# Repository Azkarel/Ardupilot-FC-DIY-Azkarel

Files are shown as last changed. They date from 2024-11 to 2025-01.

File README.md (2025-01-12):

# Ardupilot-FC-DIY-Azkarel

DIY Flight Controller for Ardupilot based on STM32H743 developer board

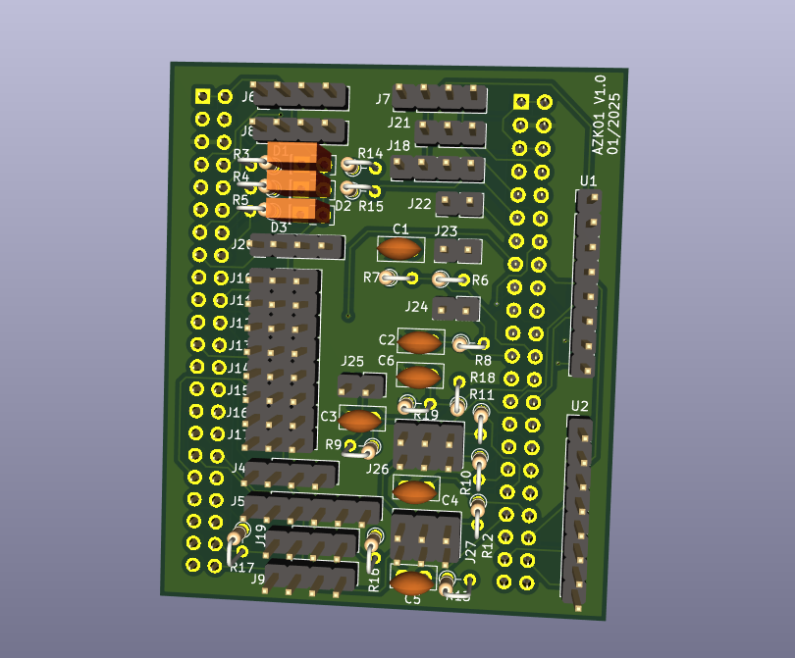
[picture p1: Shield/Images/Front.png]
AzkarelFC_Board Azkarel_Pinout


## Features

 - STM32H743 microcontroller
 - Two IMUs: MPU-9250, ICM20948
 - Two Magnetometers included in IMUs: AK8963, AK09916
 - Two Barometers: BMP-280, BMP-388
 - Internal vibration isolation for IMUs
 - Internal RGB LED
 - MicroSD card slot port
 - 1 USB port
 - 4 UARTs ports
 - 2 I2C and 1 CAN ports
 - 8 PWM output ports
 - Safety switch port
 - Buzzer port
 - RC IN port
 - SBUS/DSM port

## Pinout
AzkarelFC_Board Azkarel_Pinout

## Connectors

**GPS1**

| Pin  | Signal  | Volt  |
| :--: | :-----: | :---: |
|  1 | RX | +3.3V |
|  2 | 5V |  +5V  |
|  3 | GND |  GND  |
|  4 | TX | +3.3V |

**GPS2**

| Pin  | Signal  | Volt  |
| :--: | :-----: | :---: |
|  1 | RX | +3.3V |
|  2 | 5V |  +5V  |
|  3 | GND |  GND  |
|  4 | TX | +3.3V |

**HEATER**

| Pin  | Signal  | Volt  |
| :--: | :-----: | :---: |
|  1 |HEATER_EN| +3.3V |
|  2 | 5V |  +5V  |
|  3 | GND |  GND  |
|  4 | - |  - |

**BUZZER**

| Pin  | Signal | Volt  |
| :--: | :----: | :---: |
|  1 | 5V |  +5V  |
|  2 | GND  |  GND  |
|  3 | BUZZER | +3.3V |

**I2C2**

| Pin  | Signal  | Volt  |
| :--: | :-----: | :---: |
|  1 | I2C_SCL | +3.3V |
|  2 | 5V |  +5V  |
|  3 | GND |  GND  |
|  4 | I2C_SDA | +3.3V |

**RCINT**

| Pin  | Signal  | Volt  |
| :--: | :-----: | :---: |
|  1 |  RC_INT | +3.3V |
|  2 | 5V |  +5V  |
|  3 | GND |  GND  |
|  4 | - | - |

**PWM 1 to 8**

| Pin  |  Signal  | Volt  |
| :--: | :---: | :---: |
|  1 |  SIGNAL  | +3.3V |
|  2 | VCC |  +5V  |
|  3 | GND |  GND  |

**ADC_6V6**

| Pin  |  Signal  | Volt  |
| :--: | :---: | :---: |
|  1 | GND |  GND  |
|  2 |  SIGNAL  | +6.6V |

**ADC_3V3**

| Pin  |  Signal  | Volt  |
| :--: | :---: | :---: |
|  1 | GND |  GND  |
|  2 |  SIGNAL  | +3.3V |

**RSSI_IN**

| Pin  |  Signal  | Volt  |
| :--: | :---: | :---: |
|  1 | GND |  GND  |
|  2 |  SIGNAL  | +3.3V |

**SAFETY_LED**

| Pin  | Signal | Volt  |
| :--: | :---: | :---: |
|  1 | 5V_OUT |  +5V  |
|  2 | GND |  GND  |
|  3 | SAFETY_SW_LED | +3.3V |

**SAFETY_SW**

| Pin  | Signal | Volt  |
| :--: | :---: | :---: |
|  1 | 5V_OUT |  +5V  |
|  2 | GND |  GND  |
|  3 | SAFETY_SW | +3.3V |

**TELEM1**

| Pin  | Signal  | Volt  |
| :--: | :-----: | :---: |
|  1 | RX | +3.3V |
|  2 | 5V |  +5V  |
|  3 | GND |  GND  |
|  4 | TX | +3.3V |

**TELEM2**

| Pin  | Signal  | Volt  |
| :--: | :-----: | :---: |
|  1 | RX | +3.3V |
|  2 | TX | +3.3V |
|  3 | 5V |  +5V  |
|  4 | GND |  GND  |
|  5 | RTS | +3.3V |
|  6 | CTS | +3.3V |

**BATTERY_VOLTAGE**

| Pin  | Signal | Volt  |
| :--: | :---: | :---: |
|  1 | +5V |  GND  |
|  2 | GND |  GND  |
|  3 | BAT_VOLTAGE_ADC | +3.3V |

**BATTERY_CURRENT**

| Pin  | Signal | Volt  |
| :--: | :---: | :---: |
|  1 | +5V |  GND  |
|  2 | GND |  GND  |
|  3 | BAT_CRRENT_ADC  | +3.3V |

**I2C4**

| Pin  | Signal  | Volt  |
| :--: | :-----: | :---: |
|  1 | I2C_SCL | +3.3V |
|  2 | 5V |  +5V  |
|  3 | GND |  GND  |
|  4 | I2C_SDA | +3.3V |

**SBUS/DSM**

| Pin  | Signal  | Volt  |
| :--: | :-----: | :---: |
|  1 | RX | +3.3V |
|  2 | 5V |  +5V  |
|  3 | GND |  GND  |
|  4 | TX | +3.3V |

**USB EX**

| Pin  | Signal | Volt  |
| :--: | :----: | :---: |
|  1 | VCC_IN |  +5V  |
|  2 | DM | +3.3V |
|  3 | DP | +3.3V |
|  4 |  GND |  GND  |

## UART Mapping

 - SERIAL0 -> USB(OTG1)
 - SERIAL1 -> USART1(Telem1)
 - SERIAL2 -> USART2 (Telem2)
 - SERIAL3 -> USART3 (GPS1), NODMA
 - SERIAL4 -> UART5 (GPS2), NODMA
 - SERIAL5 -> UART8 (SBUS)
 - SERIAL6 -> UART7 (Debug), NODMA
 - SERIAL7 -> USB2(OTG2)

## RC Input

The remote control signal should be connected to the “RC IN” pin, in their specific connector.

This signal pin supports two types of remote control signal inputs, SBUS and PPM signals.

## PWM Output

The flight controller supports up to 8 PWM outputs, support all PWM protocols as well as DShot. All 8 PWM outputs have GND on the bottom row, 5V on the middle row and signal on the top row. 5V pins serves as feeding voltage for the FC from motor ESCs.

The 8 PWM outputs are in 2 groups:

 - PWM 1, 2, 3 and 4 in group1
 - PWM 5, 6, 7 and 8 in group2

Channels 1, 3, 5, 7 support bi-directional Dshot, channels 2, 4, 6, 8 support Dshot.

## Battery Monitoring

The flight controller has two connectors to monitorize voltage and current from battery.

## GPIOs

All 8 PWM channels can be used for GPIO functions (relays, buttons, RPM etc).

The pin numbers for these PWM channels in ArduPilot are shown below:

| PWM Channels | Pin  | PWM Channels | Pin  |
| --- | ---- | --- | ---- |
| PWM1 | 50 | PWM5 | 54 |
| PWM2 | 51 | PWM6 | 55 |
| PWM3 | 52 | PWM7 | 56 |
| PWM4 | 53 | PWM8 | 67 |

## Analog inputs

The flight controller has 5 analog inputs

 - ADC 5V Sense 
 - ADC Battery Current 
 - ADC Battery Voltage 
 - ADC 3V3 Sense
 - ADC 6V6 Sense
 - RSSI voltage monitoring

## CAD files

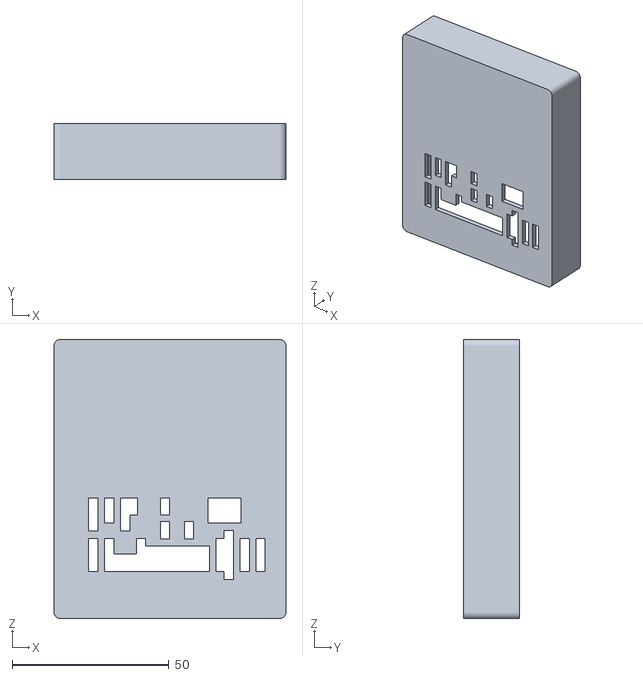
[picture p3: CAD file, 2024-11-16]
3DPrints/Tapa.STL
74.0 x 18.0 x 89.0

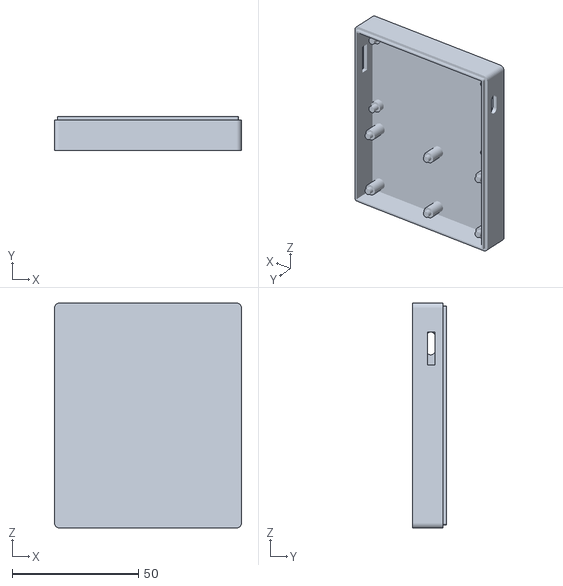
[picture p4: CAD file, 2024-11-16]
3DPrints/Base.STL
74.0 x 13.5 x 89.0

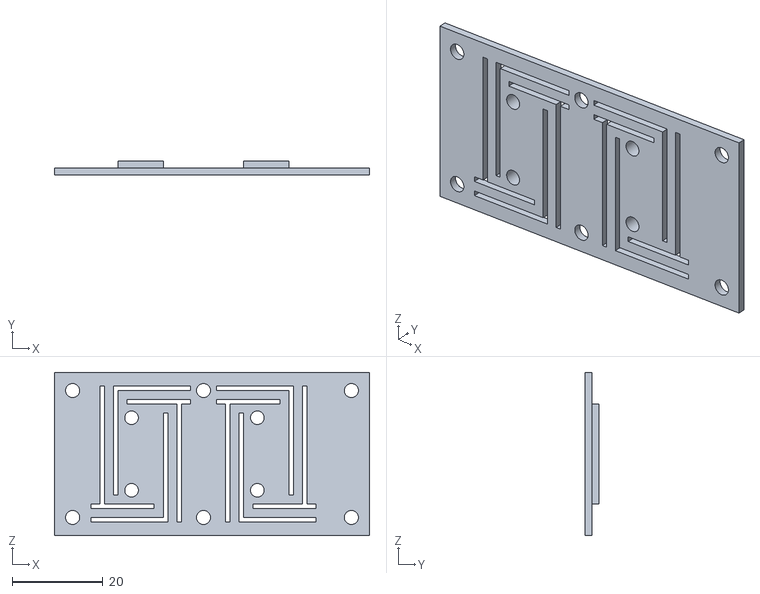
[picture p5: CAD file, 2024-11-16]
3DPrints/IMUS.STL
69.5 x 3.00 x 36.0

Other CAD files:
Shield/Shield.dxf

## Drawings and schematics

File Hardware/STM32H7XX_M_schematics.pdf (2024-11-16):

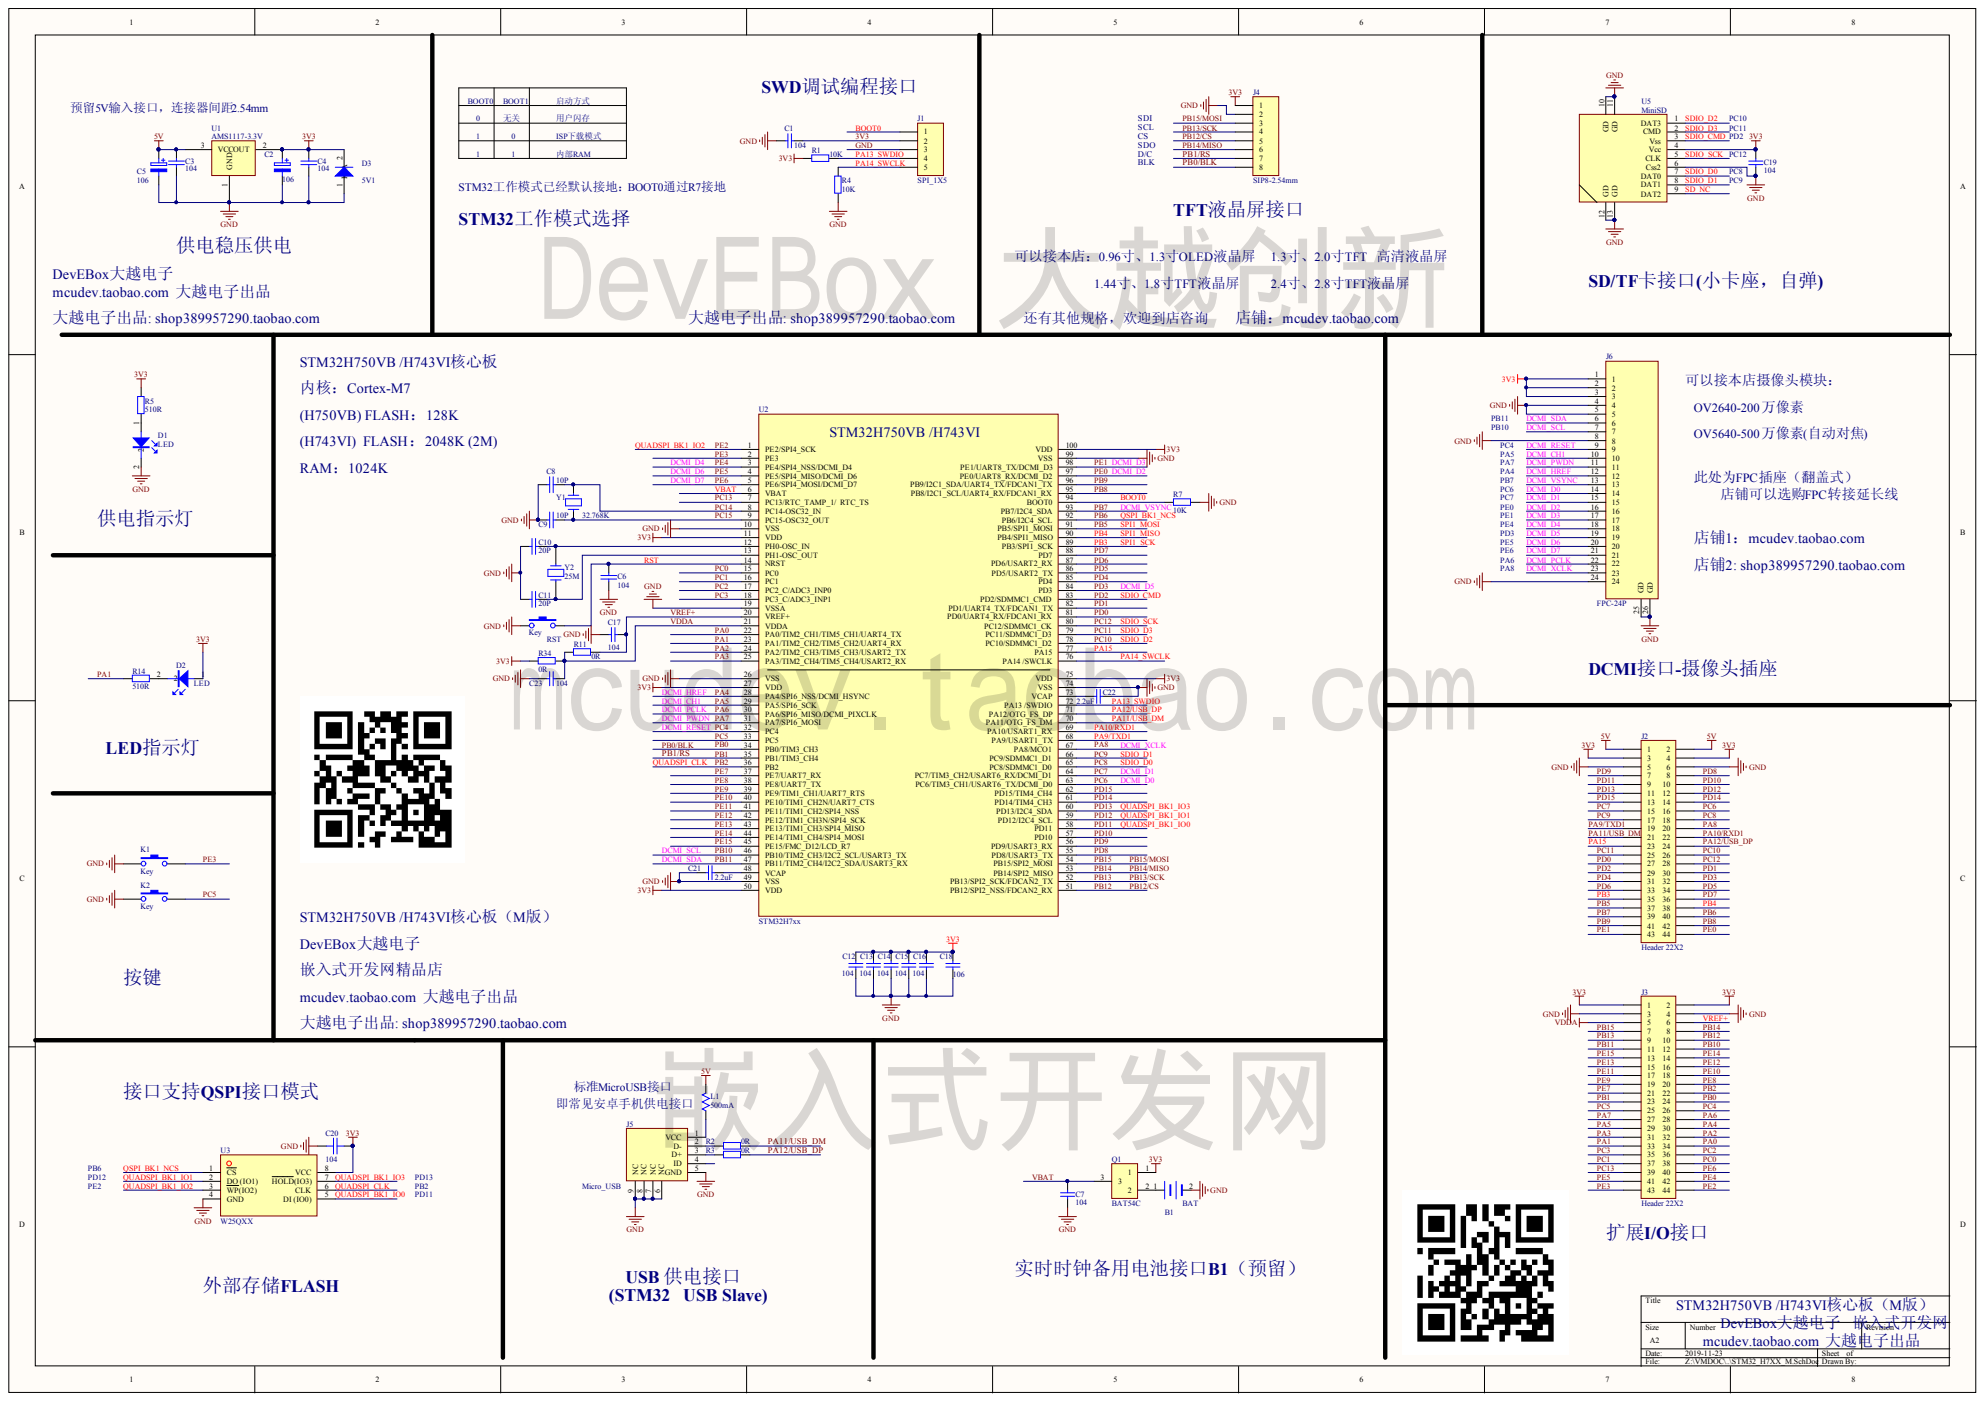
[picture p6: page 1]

GND | VSSA 19 | PD1

VCAP 48 VSS 49 | PB14

mcudev.taobao.com 大越电子出品

DevEBox大越电子

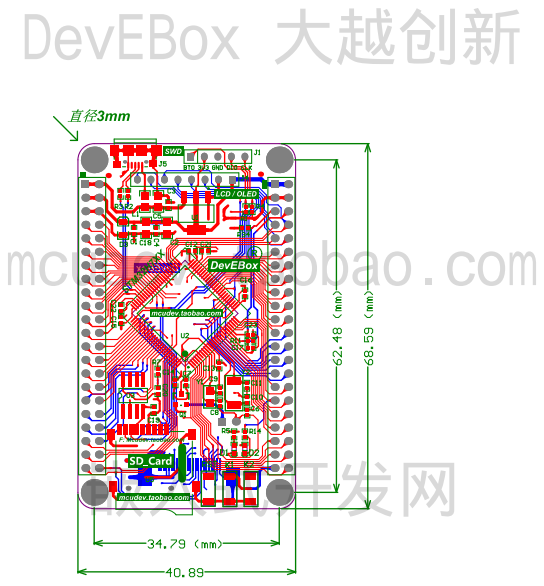
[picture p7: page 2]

Bill of Materials | <Parameter Title not found>
Source Data From: | STM32_H7XX_M.PrjPcb
Project: | | STM32_H7XX_M.PrjPcb
Variant: | | None
Creation Date: 2019-11-23 | 下午 01:44:44
Print Date: | 43792 | 43792.57279
Footprint | Comment | LibRef | Designator | Description | Quantity
SIP2-2.54mm | BAT | BATTERY | B1 | 1
RC0402 | 104 | Cap, CAP, CAP, CAP, Cap, Cap, Cap, Cap, Cap, Cap, Cap, Cap Semi, CAP, Cap | C1, C3, C4, C6, C7, C12, C13, C14, C15, C16, C17, C19, C20, C23 | Capacitor, Capacitor, Capacitor, Capacitor, Capacitor, Capacitor, Capacitor, Capacitor, Capacitor, Capacitor, Capacitor, Capacitor (Semiconductor SIM Model), [NoValue], Capacitor
14
RC0805 | 106 | ELECTRO2,
ELECTRO2,

# Cap

C2, C5, C18 | [NoValue], [NoValue], Capacitor | 3
RC0402 | 10P | CAP | C8, C9 | | 2
RC0402 | 20P | CAP | C10, C11 | Capacitor | 2
RC0603 | 2.2uF | Cap | C21, C22 | Capacitor | 2
LED-0603 | LED | LED | D1, D2 | | 2
SOD_323 | 5V1 | Diode | D3 | Default Diode | 1
SIP5-2.54mm | SPI_1X5 | Header 5H | J1 | Header, 5-Pin, Right Angle | 1
IDE2X22 | Header 22X2 | Header 22X2 | J2, J3 | Header, 22-Pin, Dual row | 2
HDR1X8 | SIP8-2.54mm | Header 8 | J4 | Header, 8-Pin | 1
micro_USB | Micro_USB | MiniUSB | J5 | | 1
FPC24- 05MM | FPC-24P | FPC-24P | J6 | | 1
SW-SPST | Key | SW-PB | K1, K2, RST | | 3
RC0805 | 500mA | RES | L1 | | 1
SOT-23- BAT54C | BAT54C | BAT54C | Q1 | | 1
RC0402 | 10K | Res2 | R1, R4, R7 | Resistor | 3
RC0402 | 0R | Res2 | R2, R3, R11, R34 | Resistor | 4
RC0402 | 510R | Res2 | R5, R14 | Resistor | 2
SOT-223 | AMS1117-3.3V | 11 | U1 | | 1
| STM32H7xx | STM32H750V | U2 | | 1
SOP8L | W25QXX | W25QXX | U3 | | 1
| MiniSD | MiniSD | U5 | | 1
JZ3215-32K | 32.768K | CRYSTAL | Y1 | 晶振 | 1
JZ5032-8M | 25M | CRYSTAL | Y2 | Crystal | 1
| | | | | 53
Approved | | Notes

# DevEBox 大越创新

# mcudev.taobao.com

# 嵌入式开发网

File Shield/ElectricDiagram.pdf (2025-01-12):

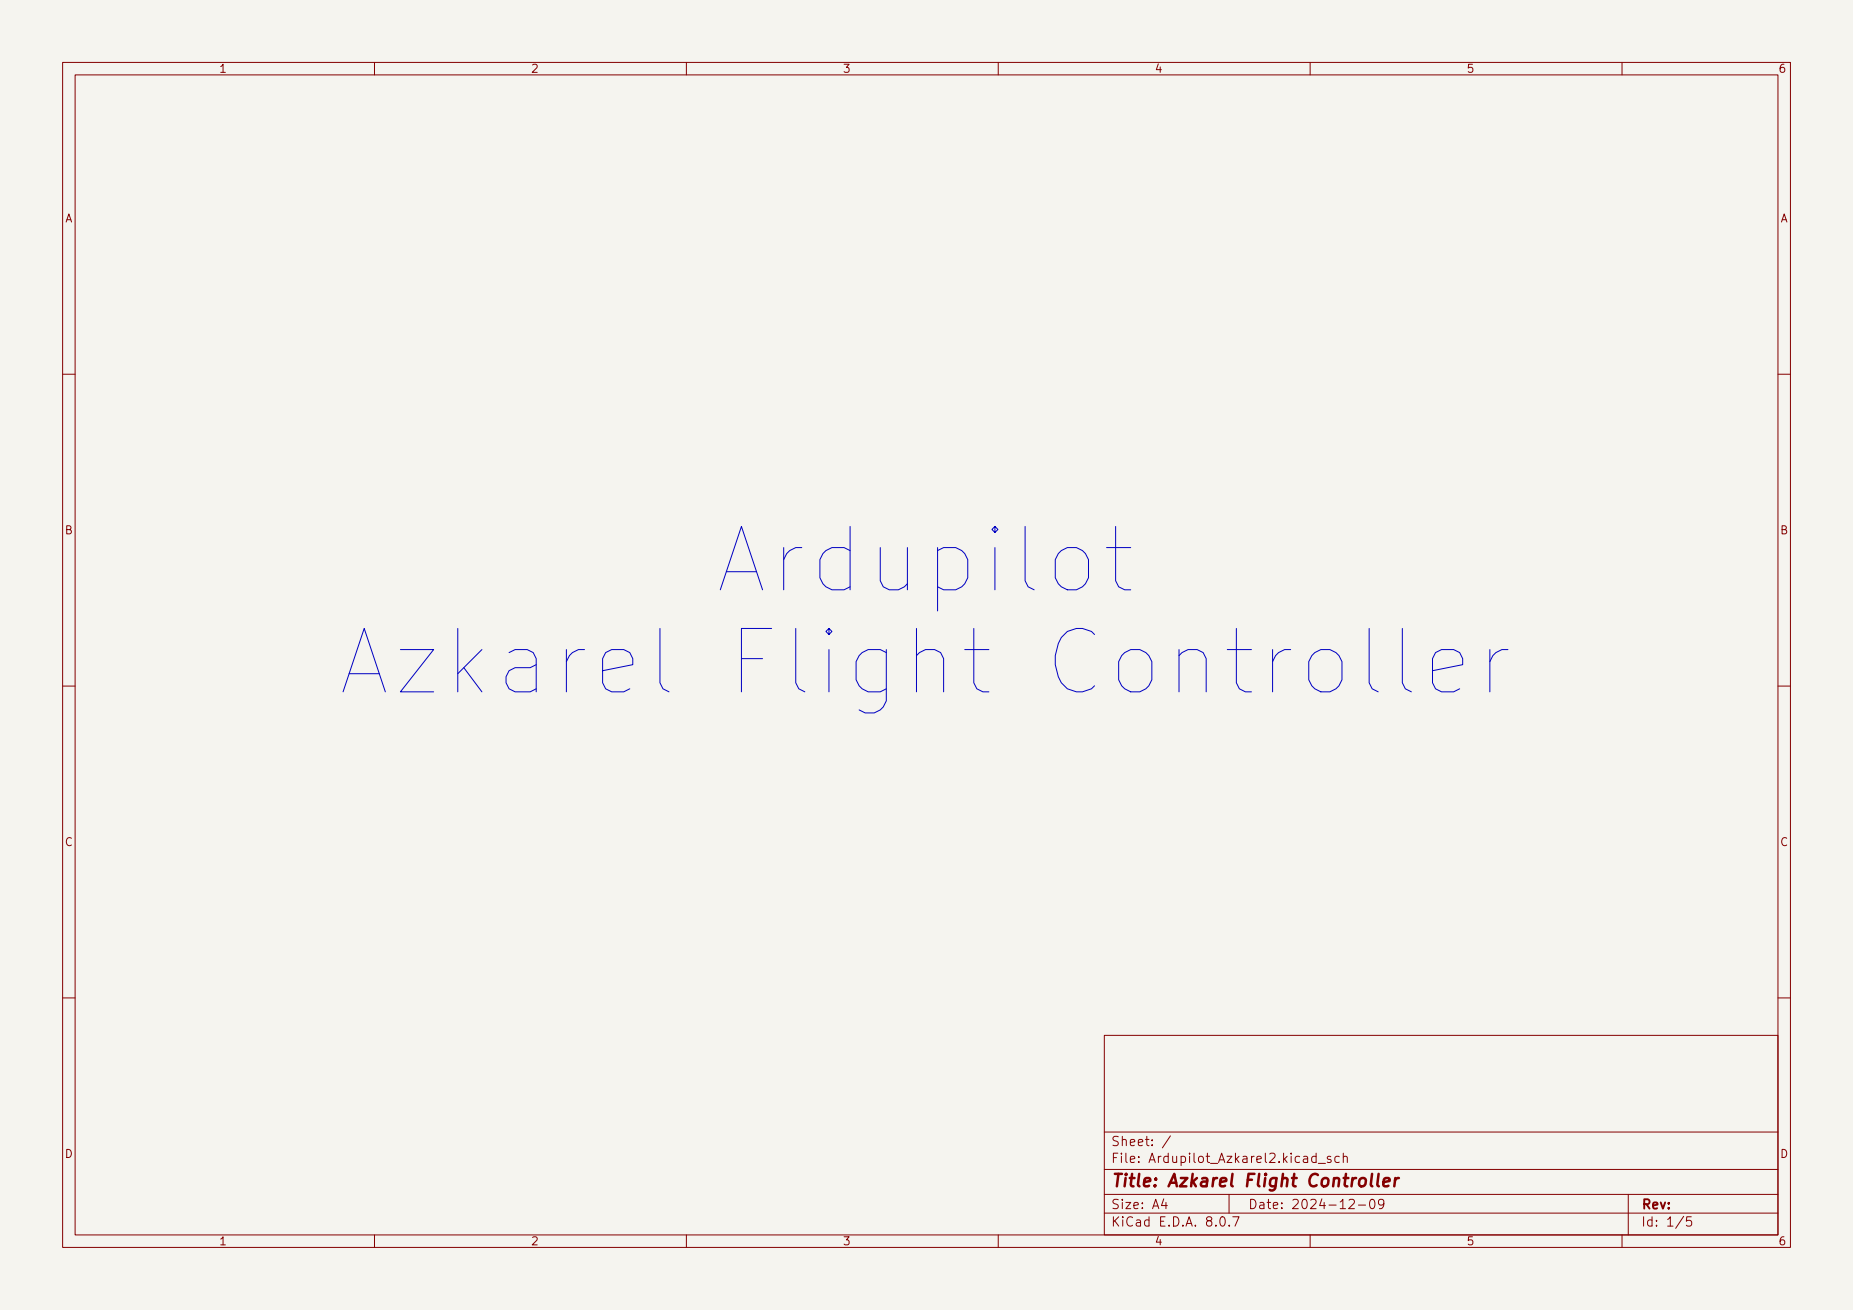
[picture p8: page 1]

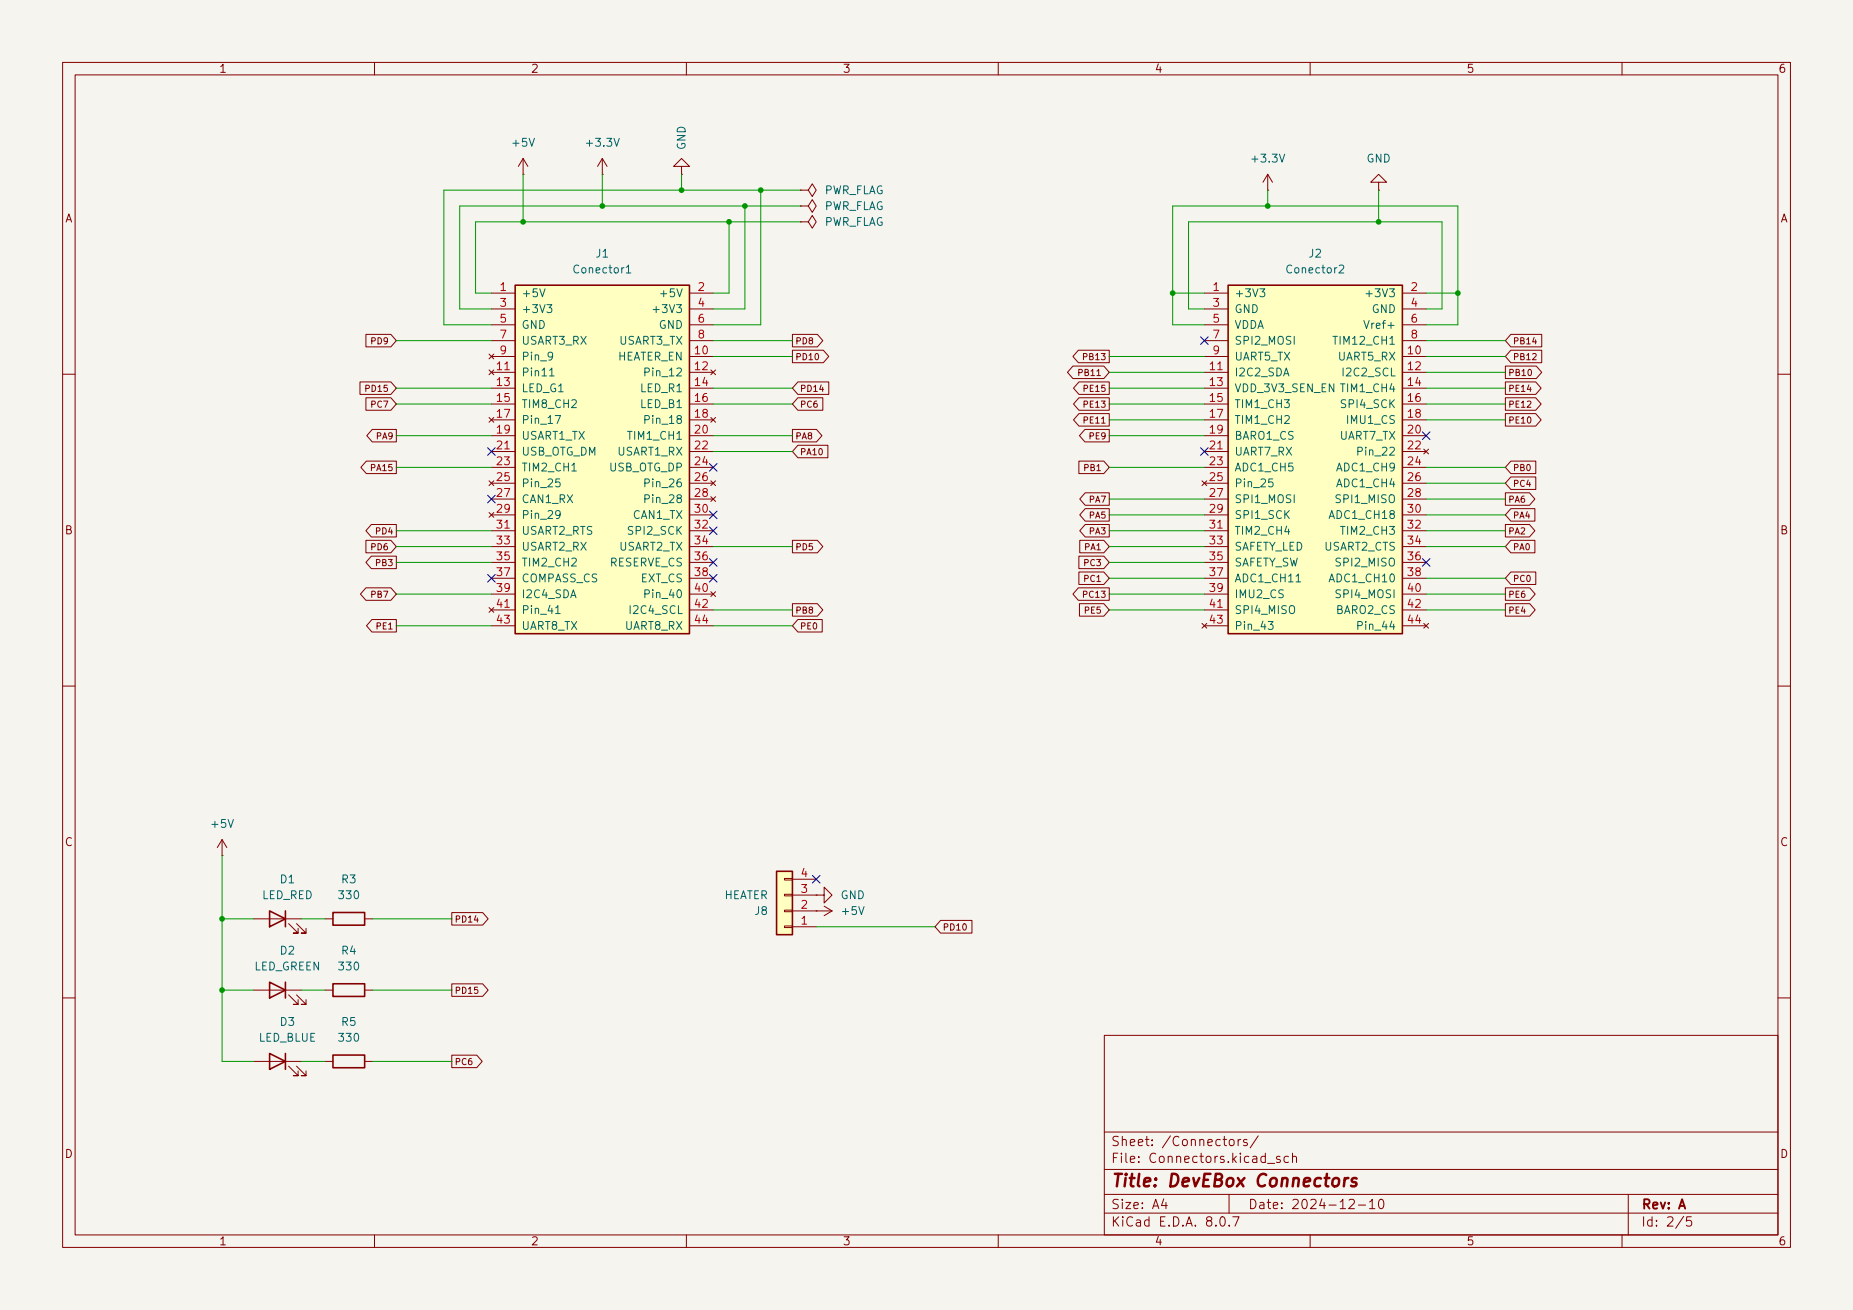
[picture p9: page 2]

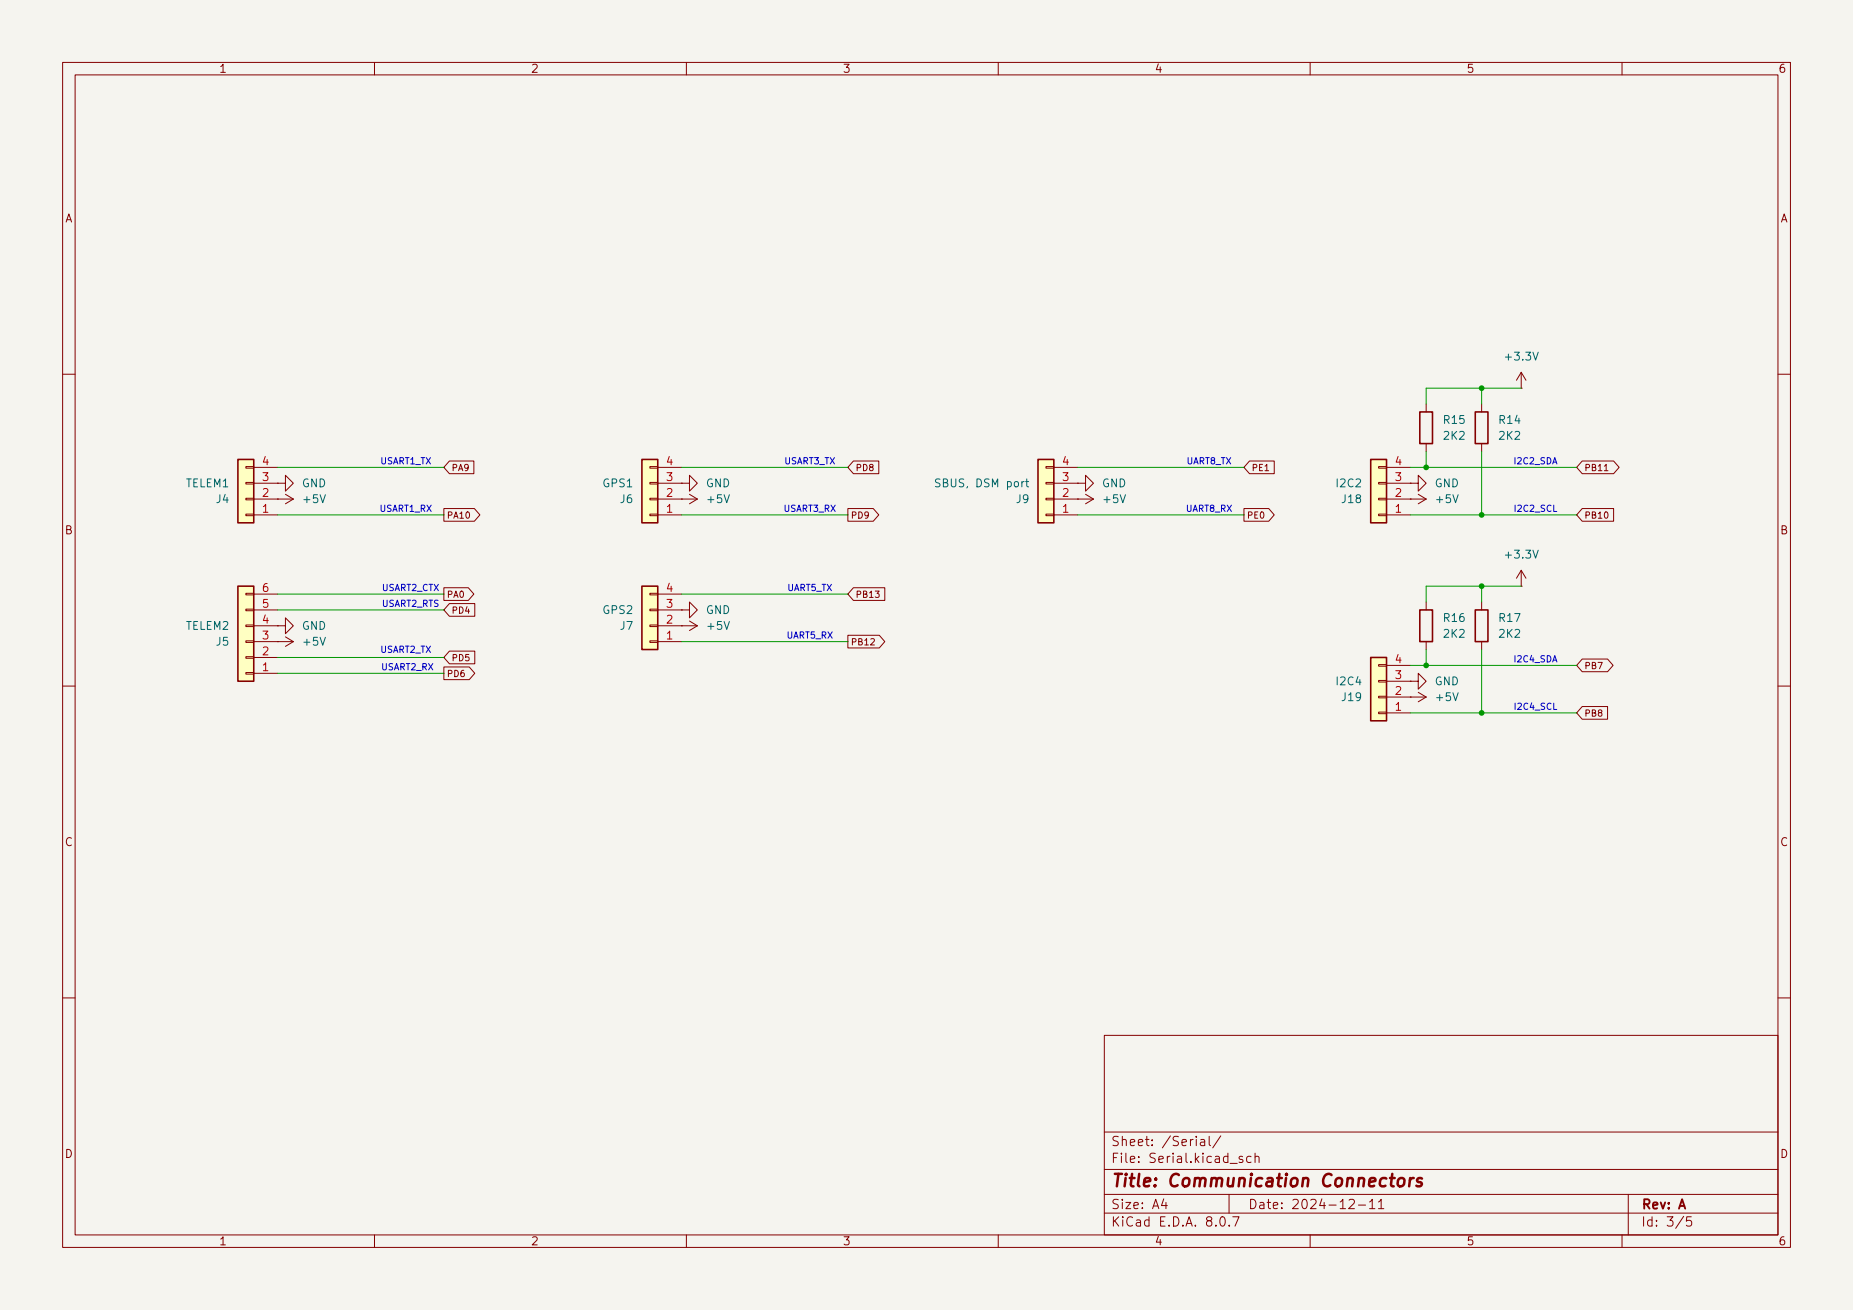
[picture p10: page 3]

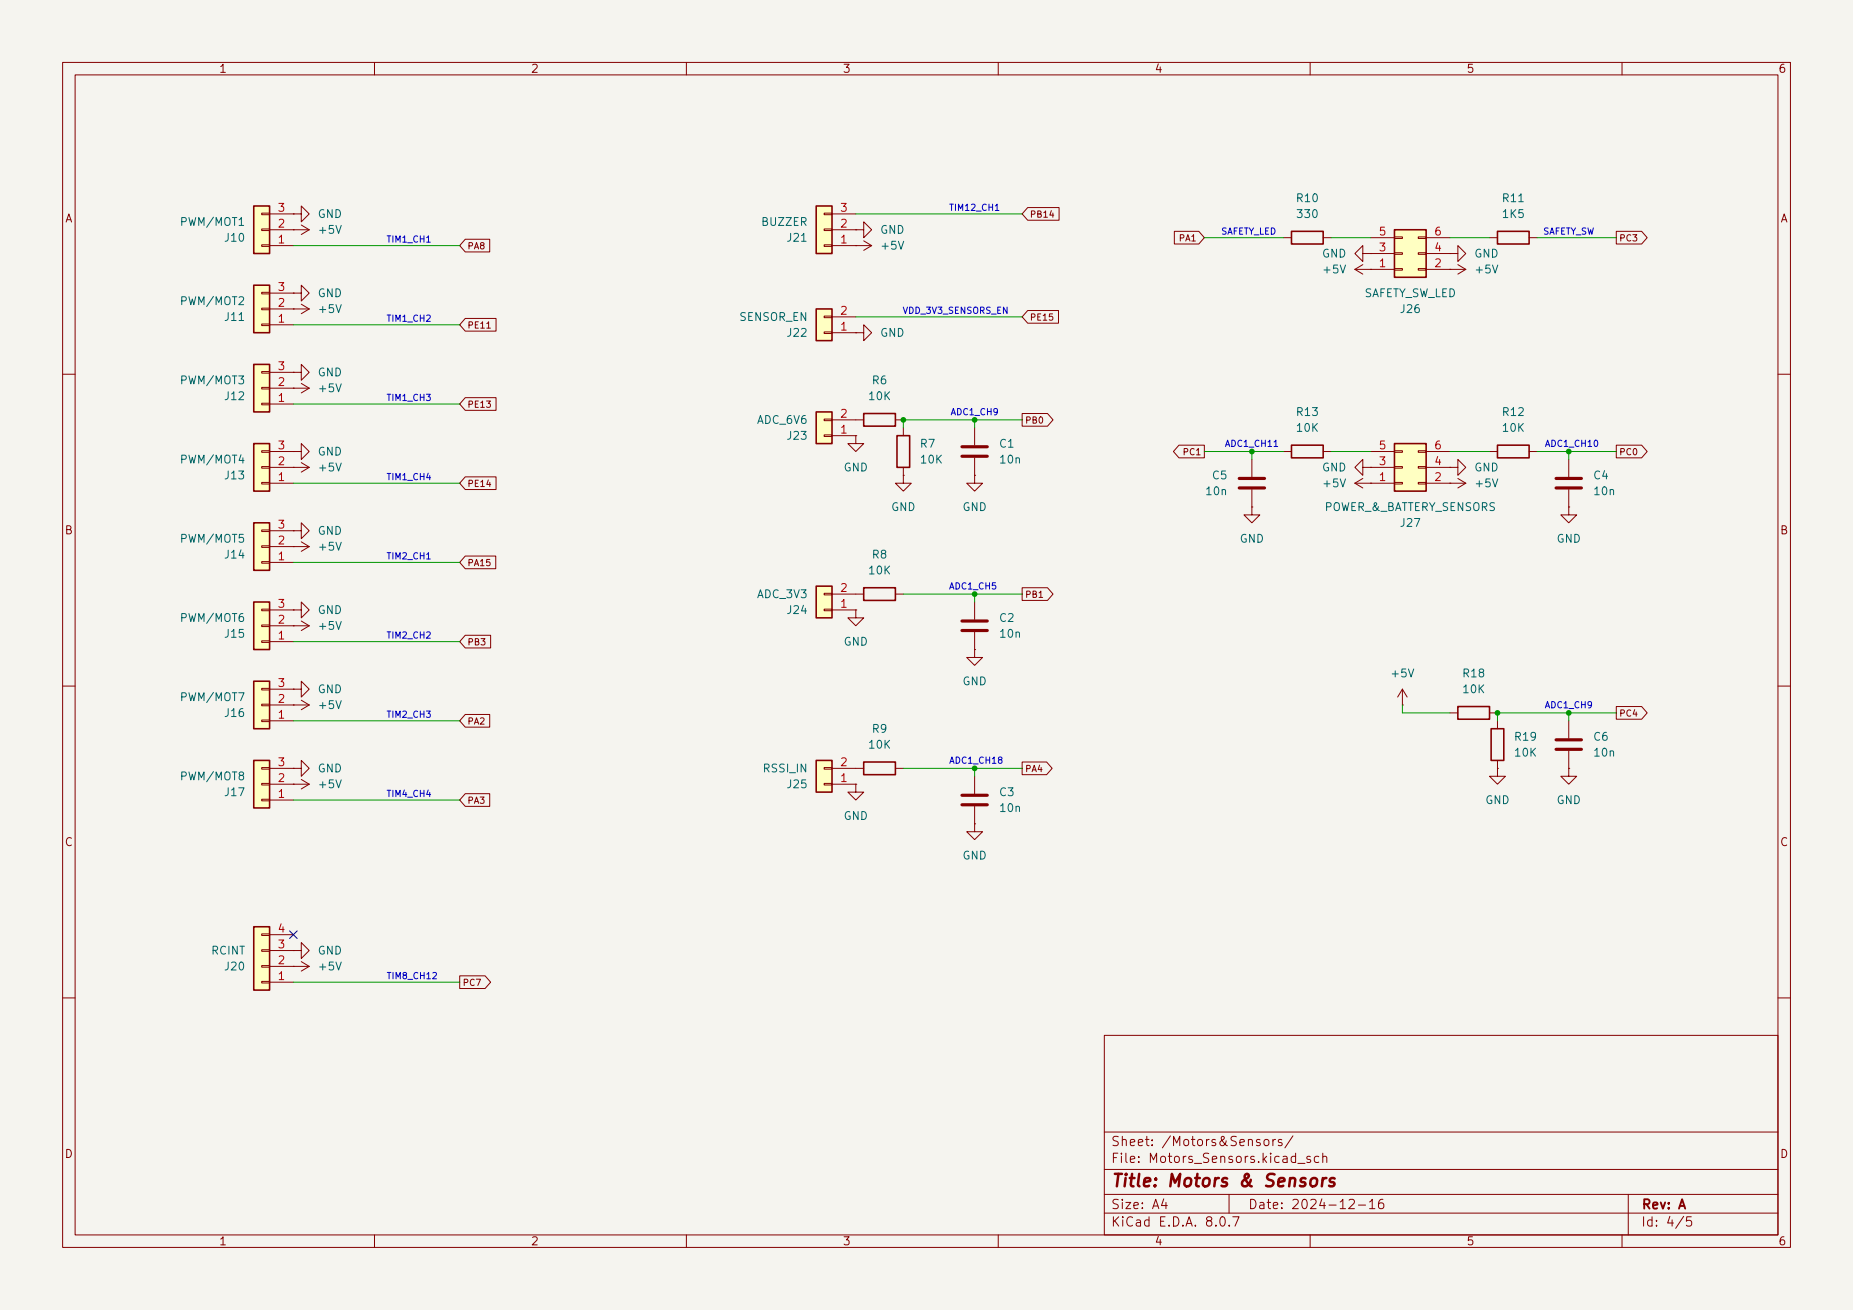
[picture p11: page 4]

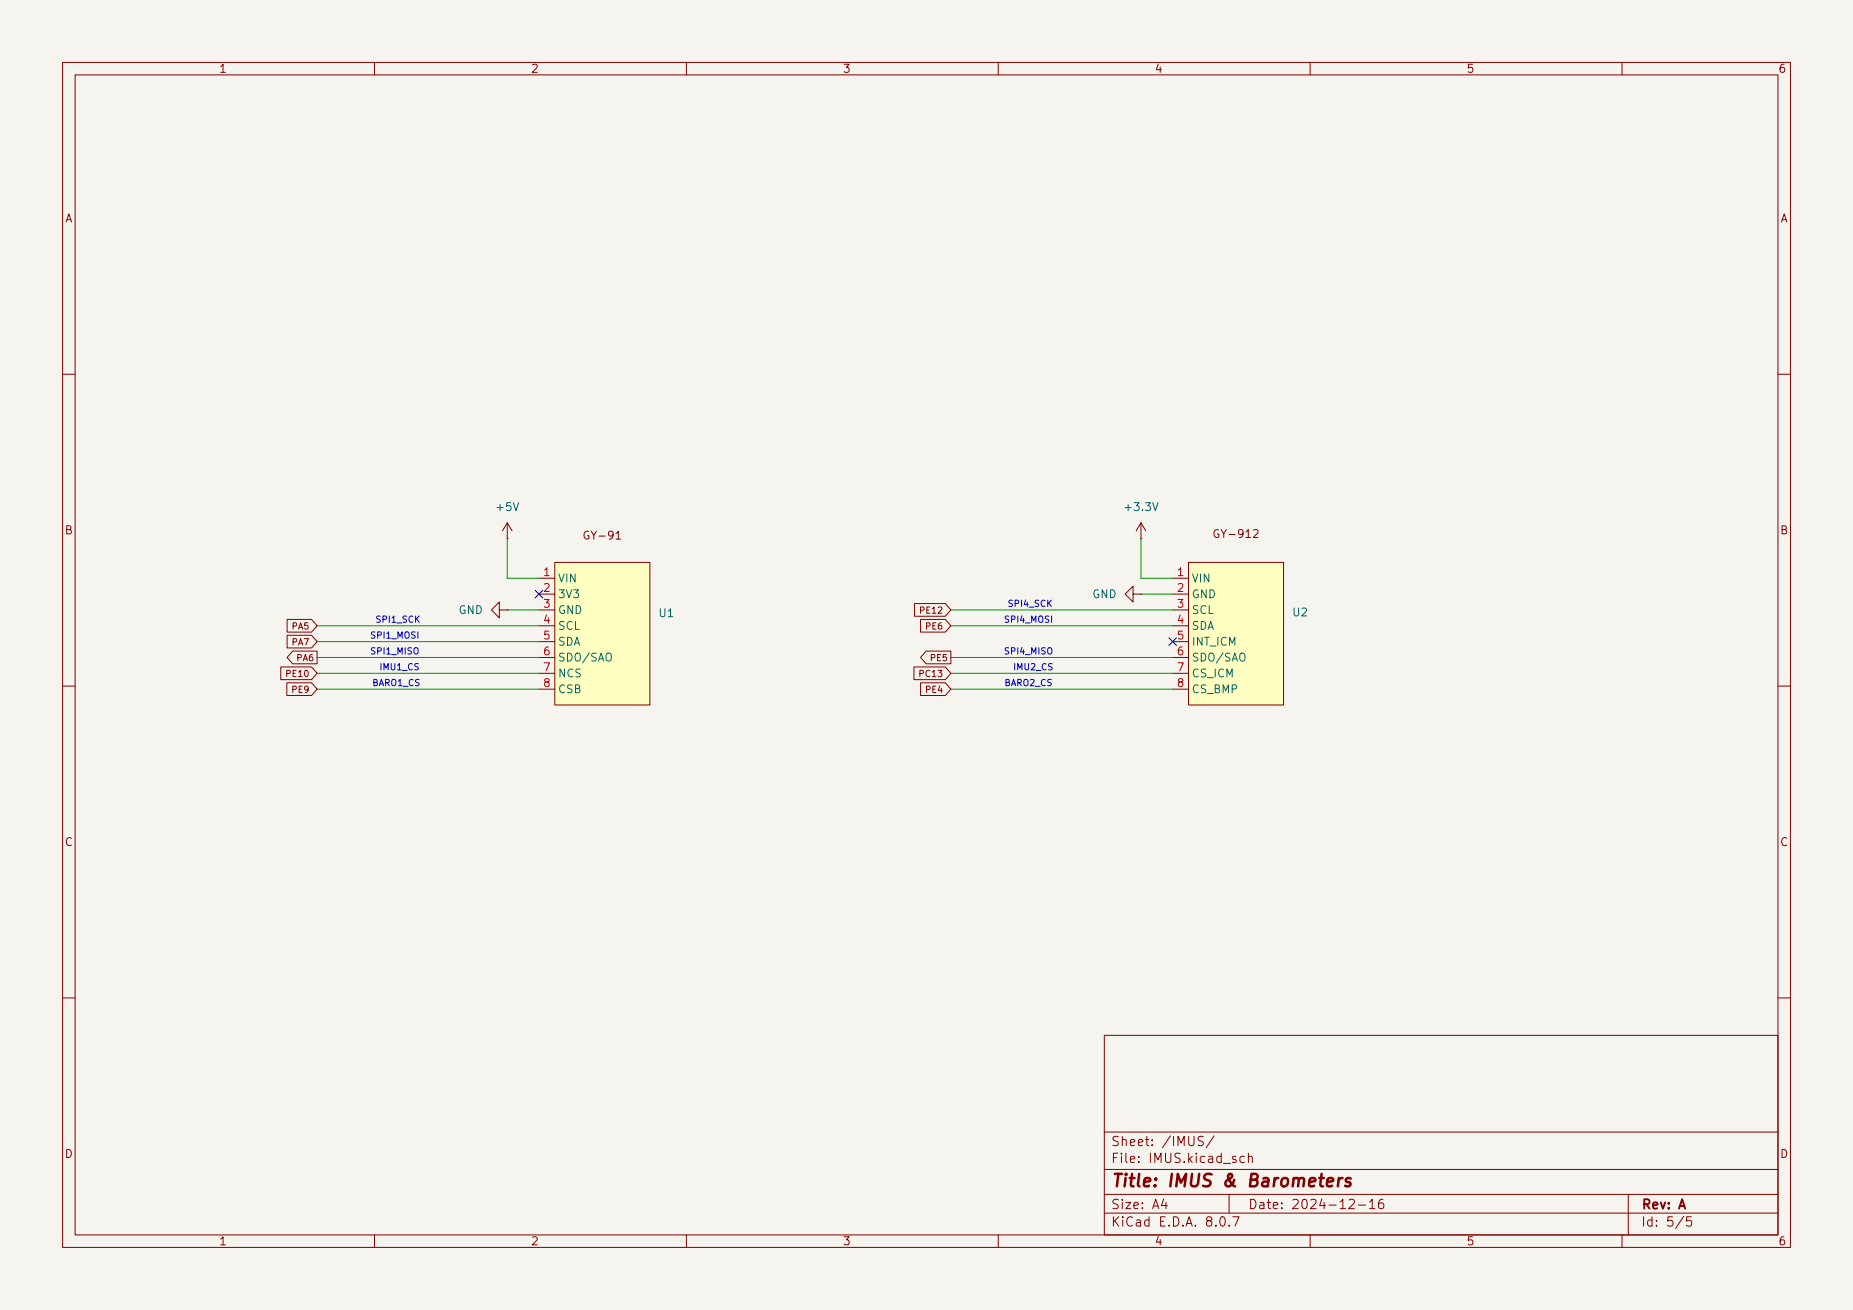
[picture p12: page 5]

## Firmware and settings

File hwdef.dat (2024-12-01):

# hw definition file for processing by chibios_hwdef.py for the AZKAREL hardware

# MCU class and specific type
MCU STM32H7xx STM32H743xx

# crystal frequency
OSCILLATOR_HZ 25000000

# board ID for firmware load
APJ_BOARD_ID 666

# flash size
FLASH_SIZE_KB 2048

# bootloader takes first sector
FLASH_RESERVE_START_KB 128

# use last 2 pages for flash storage
# H743 has 16 pages of 128k each
define HAL_STORAGE_SIZE 32768

# with 2M flash we can afford to optimize for speed
env OPTIMIZE -O2

# ChibiOS system timer
STM32_ST_USE_TIMER 5

#-------------------------------------------------------------------------------

# order of UARTs (and USB)
SERIAL_ORDER OTG1 USART1 USART2 USART3 UART5 UART7 UART8

# now we define the pins that USB is connected on
PA11 OTG_FS_DM OTG1
PA12 OTG_FS_DP OTG1

# USART1 TELEM1
PA9  USART1_TX USART1
PA10 USART1_RX USART1

# USART2 TELEM2
PA0  USART2_CTS_NSS USART2
PD4  USART2_RTS USART2
PD5  USART2_TX USART2
PD6  USART2_RX USART2

# USART3 GPS
PD8  USART3_TX USART3 NODMA
PD9  USART3_RX USART3 NODMA

# UART5 GPS2
PB12 UART5_RX UART5 NODMA
PB13 UART5_TX UART5 NODMA

# UART7 DEBUG
PE7  UART7_RX UART7 NODMA
PE8  UART7_TX UART7 NODMA

# SBUS, DSM port
PE0  UART8_RX UART8
PE1  UART8_TX UART8

# these are the pins for SWD debugging with a STlinkv2 or black-magic probe
PA13 JTMS-SWDIO SWD
PA14 JTCK-SWCLK SWD

#-------------------------------------------------------------------------------

# SPI1 -IMU1 -BARO1
PA5  SPI1_SCK SPI1
PA6  SPI1_MISO SPI1
PA7  SPI1_MOSI SPI1

# SPI2 for future use in next editions
# PD3  SPI2_SCK SPI2
# PC2  SPI2_MISO SPI2
# PB15 SPI2_MOSI SPI2

# SPI4 -IMU2 -BARO2
PE12 SPI4_SCK SPI4
PE5  SPI4_MISO SPI4
PE6  SPI4_MOSI SPI4

# sensors cs
PE10 IMU1_CS CS
PE9  BAROMETER1_CS CS
PC13 IMU2_CS CS
PE4  BAROMETER2_CS CS
PB5  COMPASS_CS CS
PD7  RESERVE_CS CS

# Extra SPI CS
PB4  EXT_CS CS

#-------------------------------------------------------------------------------

# order of I2C buses
I2C_ORDER I2C2 I2C4

# I2C buses
PB10 I2C2_SCL I2C2
PB11 I2C2_SDA I2C2

PB8  I2C4_SCL I2C4
PB7  I2C4_SDA I2C4

# no built-in compass, but probe the i2c bus for all possible
# external compass types
define ALLOW_ARM_NO_COMPASS
define HAL_PROBE_EXTERNAL_I2C_COMPASSES
define HAL_I2C_INTERNAL_MASK 0
define HAL_COMPASS_AUTO_ROT_DEFAULT 2

# NODMA I2C*
# define STM32_I2C_USE_DMA FALSE

# This defines the default maximum clock on I2C devices
# define HAL_I2C_MAX_CLOCK 100000

#-------------------------------------------------------------------------------

# CAN bus for future use in next editions
# PD0  CAN1_RX CAN1
# PD1  CAN1_TX CAN1

#-------------------------------------------------------------------------------

# PWM channels
PA8  TIM1_CH1  TIM1 PWM(1)  GPIO(50)
PE11 TIM1_CH2  TIM1 PWM(2)  GPIO(51)
PE13 TIM1_CH3  TIM1 PWM(3)  GPIO(52)
PE14 TIM1_CH4  TIM1 PWM(4)  GPIO(53)
PA15 TIM2_CH1  TIM2 PWM(5)  GPIO(54)
PB3  TIM2_CH2  TIM2 PWM(6)  GPIO(55)
PA2  TIM2_CH3  TIM2 PWM(7)  GPIO(56)
PA3  TIM2_CH4  TIM2 PWM(8)  GPIO(57)

# RC input
PC7  TIM8_CH2 TIM8 RCININT PULLUP LOW

# PWM output for buzzer
PB14 TIM12_CH1 TIM12 GPIO(77) ALARM

#-------------------------------------------------------------------------------

# Analog in
PC0  BATT_CURRENT_SENS ADC1 SCALE(1)
PC1  BATT_VOLTAGE_SENS ADC1 SCALE(1)

PC4  VDD_5V_SENS ADC1 SCALE(2)
PA4  RSSI_IN ADC1 SCALE(1)

# ADC3.3/ADC6.6
PB0  SPARE1_ADC1 ADC1 SCALE(2)
PB1  SPARE2_ADC1 ADC1 SCALE(1)

#------------------------------------------------------------------------------

# GPIOs
PD10 HEATER_EN OUTPUT LOW GPIO(80)
define HAL_HEATER_GPIO_PIN 80
define HAL_HAVE_IMU_HEATER 0

# enable pins
PE15  VDD_3V3_SENSORS_EN OUTPUT LOW

# TriColor LED, Red, Green, Blue
define AP_NOTIFY_GPIO_LED_RGB_ENABLED 1

# LED setup
PD15 LED_R1 OUTPUT OPENDRAIN HIGH GPIO(0)
PD14 LED_G1 OUTPUT OPENDRAIN HIGH GPIO(1)
PC6  LED_B1 OUTPUT OPENDRAIN HIGH GPIO(2)

define AP_NOTIFY_GPIO_LED_RGB_RED_PIN 0
define AP_NOTIFY_GPIO_LED_RGB_GREEN_PIN 1
define AP_NOTIFY_GPIO_LED_RGB_BLUE_PIN 2

# allow to have have a dedicated safety switch pin
define HAL_HAVE_SAFETY_SWITCH 1
PA1  LED_SAFETY OUTPUT
PC3  SAFETY_IN INPUT PULLDOWN

#-------------------------------------------------------------------------------

# SPI devices
SPIDEV mpu9250      SPI1 DEVID1  IMU1_CS         MODE3  2*MHZ   4*MHZ
SPIDEV icm20948     SPI4 DEVID3  IMU2_CS         MODE3  2*MHZ   4*MHZ
SPIDEV bmp280       SPI1 DEVID2  BAROMETER1_CS   MODE3  1*MHZ   8*MHZ
SPIDEV bmp388       SPI4 DEVID4  BAROMETER2_CS   MODE3  5*MHZ   10*MHZ

# IMU1
IMU     Invensense SPI:mpu9250 ROTATION_YAW_270
COMPASS AK8963:probe_mpu9250 0 ROTATION_PITCH_180

# IMU2
IMU     Invensensev2 SPI:icm20948 ROTATION_YAW_270
COMPASS AK09916:probe_ICM20948 0 ROTATION_ROLL_180_YAW_90

# define HAL_DEFAULT_INS_FAST_SAMPLE 5

# BARO1
BARO    BMP280 SPI:bmp280

# BARO2
BARO    BMP388 SPI:bmp388

#-------------------------------------------------------------------------------

# microSD support
PC8  SDMMC1_D0 SDMMC1
PC9  SDMMC1_D1 SDMMC1
PC10 SDMMC1_D2 SDMMC1
PC11 SDMMC1_D3 SDMMC1
PC12 SDMMC1_CK SDMMC1
PD2  SDMMC1_CMD SDMMC1

# enable FAT filesystem support (needs a microSD defined via SDMMC)
define HAL_OS_FATFS_IO 1

#--------------------------------------------------------------------------------

# DMA definitions
DMA_PRIORITY SPI1* SPI4* TIM*UP*
DMA_NOSHARE SPI1* SPI4* TIM*UP*

#--------------------------------------------------------------------------------

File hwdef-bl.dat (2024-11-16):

# hw boot loader definition file for processing by chibios_hwdef.py
# for the AZKAREL hardware

# MCU class and specific type
MCU STM32H7xx STM32H743xx

# crystal frequency
OSCILLATOR_HZ 25000000

# board ID for firmware load
APJ_BOARD_ID 666

# flash size
FLASH_SIZE_KB 2048

# bootloader is installed at zero offset
FLASH_RESERVE_START_KB 0

# the location where the bootloader will put the firmware
# the H743 has 128k sectors
FLASH_BOOTLOADER_LOAD_KB 128

env OPTIMIZE -Os

# order of UARTs (and USB)
SERIAL_ORDER OTG1

# USB
PA11 OTG_FS_DM OTG1
PA12 OTG_FS_DP OTG1

# pins for SWD debugging
PA13 JTMS-SWDIO SWD
PA14 JTCK-SWCLK SWD

# Add CS pins to ensure they are high in bootloader
PE10 IMU1_CS CS
PE9  BAROMETER1_CS CS
PC13 IMU2_CS CS
PE4  BAROMETER2_CS CS
PB5  COMPASS_CS CS
PD7  RESERVE_CS CS

# Extra SPI CS
PB4  EXT_CS CS

PA1 LED_BOOTLOADER OUTPUT LOW
define HAL_LED_ON 0

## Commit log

2024-11-16 First Edition
    [defaults.parm]
2024-11-16 Modified Tapa
    [Tapa.STL]
2024-11-16 Modified Shield with some 5V contacts more
    [Shield.dxf, shield3_pin_description.ods]
2024-11-16 Modified Shield with some more 5v contacts
2024-11-16 Some 5V more contacts.md
2025-01-12 Delete Shield/EsquemaKiCad.zip
    New KiCad files developed
2025-01-12 Delete Shield/Esquema.pdf
    New KiCad Files developed
2025-01-12 New KiCad files developed
